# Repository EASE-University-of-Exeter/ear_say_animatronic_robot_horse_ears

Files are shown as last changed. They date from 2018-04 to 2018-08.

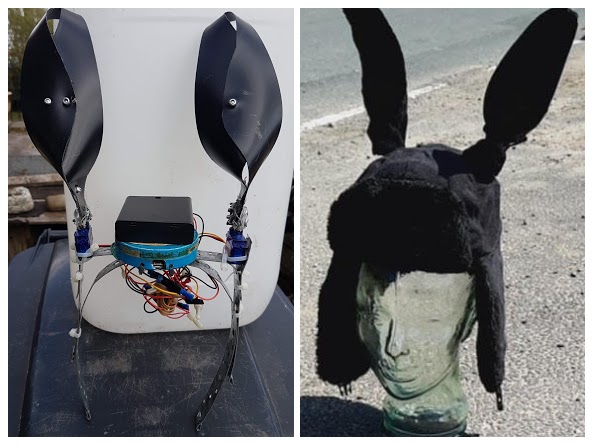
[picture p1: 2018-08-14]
umamimi robotic horse ears - with and without cover.jpg

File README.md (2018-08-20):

umamimi_robotic_horse_ears

================

Author:  Steve North

Author URI:  http://socialsciences.exeter.ac.uk/sociology/staff/north/

License: AGPLv3 or later

License URI: http://www.gnu.org/licenses/agpl-3.0.en.html

Can: Commercial Use, Modify, Distribute, Place Warranty

Can't: Sublicence, Hold Liable

Must: Include Copyright, Include License, State Changes, Disclose Source

Copyright (c) 2018, The University of Exeter

Exploring what it means to be a horse, using expressive ears to communicate both intention and emotion. 

Inspired by the Japanese tradition called ‘Kemonomimi’ (animal eared), which is found in both anime and manga.

This is a project that will reflect on the making of robotic horse ears, living amongst horses using the ears, interspecies communication, becoming 'horse' and even the nature of the quantitative studies that might be conducted to evaluate this artefact.

Umamimi is also inspired by the machines developed for animatronic and puppetry performances. 

Built on a metal framework, with black faux fur covering, two micro servo motors each move an ear independently, in incremental steps, through a maximum range of 180 degrees. An ATmega32u4 processor has been programmed in the Arduino language (a set of C/C++ functions). When the user makes small changes in the inclination of her head, Umamimi’s built-in accelerometer sends these to the software, which responds with programmed (and fully customisable) ear movements: fully forward, fully back, either ear turned outward. When in neutral (meaning that the accelerometer and therefore the device is level), a range of random default ear flicks and movements have been specified.

Horses with different personalities may be configured by selecting a header file (see default.h for a template).

The configurable parameters are as follows:

// Params for random micro default ear movements (when not specifically triggered for specific movement behaviour)

#define PERCENTAGE_TIME_EARS_STATIC 90 // range 1-100% - % of time ears are static

#define DELAY_BETWEEN_EACH_STEP_WHEN_EAR_MOVING 10 // Ear travel time (break each movement into steps and specify pause length between steps)

#define PERCENTAGE_EAR_RANDOM_MICRO_MOVES_TENDING_TOWARDS_UPPER_LIMIT_OF_RANGE 50 // % of ear movements that tend towards upper limits of preset range 

PSEUDOCODE

Loop () 

	{  // Start loop which checks for accelerometer position

	Get the accelerometer position from the microprocessor
	if (position is outside a given threshold limits for pitch and roll - user's head orientation changes triggers ear movement)
		{
			Do something appropriate with one or more ears: move both front, move both back rotate a single ear to outside
		}

	else  // accelerometer position is level /centred or within threshold limits for pitch and roll
		{ 
		
		if (JUST_USER_TRIGGERED_MOVEMENTS)
			{
				new servo/ear positions = defined centre positions for ears
			}
		else // use random micro movements... this is the random microMove algorithm (the automatic ear moves made when the accelerometer is centred)
			{
				Get a random number between 1 and 100
				if (random number > PERCENTAGE_TIME_EARS_STATIC)
					{
						Get a random number between 1 and 100
						if (random number > PERCENTAGE_EAR_RANDOM_MICRO_MOVES_TENDING_TOWARDS_UPPER_LIMIT_OF_RANGE) // restricts the number of higher values, by weighting in favour of lower random values
							{
								restrict RANGE_FOR_RANDOM_MICRO_ANIMATIONS_RELATIVE_TO_CENTRED by the defined ATTENUATION_FACTOR_FOR_MICRO_MOVES_RANGE
							}
						else // choose a random ear position that is within the full RANGE_FOR_RANDOM_MICRO_ANIMATIONS_RELATIVE_TO_CENTRED without 
							{
								Use the full RANGE_FOR_RANDOM_MICRO_ANIMATIONS_RELATIVE_TO_CENTRED
							}
						new servo/ear position = a random number between 1 and 100 and map this to a value in the (full or restricted) RANGE_FOR_RANDOM_MICRO_ANIMATIONS_RELATIVE_TO_CENTRED
					} // close random number was outside PERCENTAGE_TIME_EARS_STATIC... So, generate a random micromove
			
				else // random number was inside PERCENTAGE_TIME_EARS_STATIC
					{
						new servo/ear positions = defined centre positions for ears
					}
	 
			} // use random micro movements
		
		} // close accelerometer position is level /centred or within threshold limits for pitch and roll
		
	if (the new servo/ear positions are the same as the last positions)
		{
			don't move to the same place! // it's a waste of battery life and the wears the servos
		}
	else // the new servo/ear positions are different from the last positions
		{
		if (the new servo/ear positions are user triggered moves / changes in the accelerometer OR the accelerometer is centred immediately after a user triggered move)
			{
				move servos to the new positions (immediately) // this is to make the device responsive to user input, even if the parameters have configured a laconic horse
			}
		else // the moves are random micro movements
			{
				move servo from the previous position to the new position, incrementally with a delay between each increment determined by DELAY_BETWEEN_EACH_STEP_WHEN_EAR_MOVING
			}
		} // close the new servo/ear positions are different from the last positions
	
	} // close loop which checks for accelerometer position

Umamimi - coding setup and config - Arduino IDE and libraries

1. Install Arduino IDE (for Windows, I used: arduino-1.8.5-windows.exe)
2. Install the Adafruit TiCoServo library v1.0.1 in Arduino IDE 1.8.5, do this: Sketch > Include Library > Manage Libraries > search for TiCo and then click Install
Note: Adafruit Circuit Playground v.1.6.8 should be pre-installed in Arduino IDE v.1.8.5
Note: these need to included at the start of a sketch with:
#include <Adafruit_CircuitPlayground.h>
#include <Adafruit_TiCoServo.h>
Note: if needing to test Circuit Playground from Arduino IDE, see File > Examples > Adafruit Circuit Playground
3. To edit Umamimi Robotic Horse ears code, load the sketch umamimi_robotic_horse_ears.ino from the cloned GitHub repository.
4. To connect the Adafruit Circuit Playground in the robotic ears to Arduino IDE (in order to upload the compiled code(, do: Tools > Board > Adafruit Circuit Playground
5. Then do: Tools > Port > <The USB port that the Circuit Playground is connected to. For example: 'COM3 (Adafruit Circuit Playground)'

Umamimi parts list for hardware

1 x AdaFruit Circuit Playground Classic (all-in-one board that has sensors and LEDs)
2 x Tower Pro SG92R Digital Micro Servo
1 x Battery Holder with On/Off Switch for 4 x AA batteries
1 x 2-Pin Male JST-XH Balance Connector with extension wire
1 x Black Micro Suede Trapper Hat
Wire in different colours: 22AWG stranded, outer diameter 1.6mm.
Firm plastic to provide ear shape and rigidity - I upcycled the plastic covers from ringbinder files
1 x metre length of 100% Cotton Velvet - Black - Fabric Velveteen - for ear covering
Velcro tape - to secure inner lining of trapper hat, after opening has been made to insert the device skeleton
Small, elderly, circular metal sticky tape tin (or similar) - to house the Circuit Playground
A roll of metal builders’ band - for umamimi skeleton / head band
Cable ties (with a width narrow enough to go through the holes in the builders’ band) - to fix parts of the skeleton together and to attach the servos, battery holder and Circuit Playground container to the skeleton
Glue gun for ear plastic shaping, sticking black velvet to plastic ears shapers, attaching the servo horn to the ears etc..
Rivet gun - to hold the plastic ear shapers in the stressed ear position (glue on its own didn’t hold!)

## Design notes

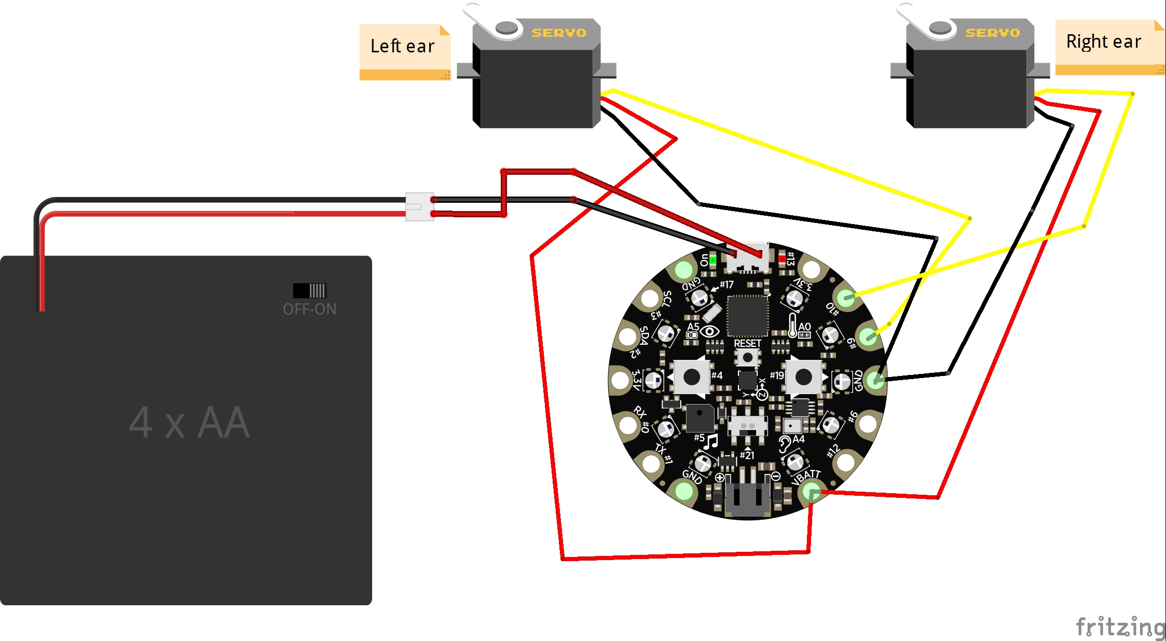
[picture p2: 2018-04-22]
umamimi_robotic_horse_ears- circuit diagram.jpg

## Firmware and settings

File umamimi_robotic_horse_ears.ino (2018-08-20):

/*
umamimi_robotic_horse_ears
================
Author:  Steve North
Author URI:  http://socialsciences.exeter.ac.uk/sociology/staff/north/
License: AGPLv3 or later
License URI: http://www.gnu.org/licenses/agpl-3.0.en.html
Can: Commercial Use, Modify, Distribute, Place Warranty
Can't: Sublicence, Hold Liable
Must: Include Copyright, Include License, State Changes, Disclose Source

Copyright (c) 2018, The University of Exeter
*/

// Leave one (and only one!) of the below horse config files below uncommented, 
// to set random behaviour when centred to a particular horse personality / mood.
// Using default.h as a template. create your own horse and add its profile here.
// For example: dapples.h

// ######### HORSE CONFIG FILES #####################################

#include "default.h"
//#include "free.h"
//#include "duke.h"
//#include "tashe.h"
//#include "smokie.h"
//#include "test_horse_1.h"
//#include "profile_edit_test.h"

// ######### HORSE CONFIG FILES #####################################



#include <Adafruit_CircuitPlayground.h>
#include <Adafruit_TiCoServo.h>

// set next true to turn off randomMicroMovements when accelerometer is centred
#define JUST_USER_TRIGGERED_MOVEMENTS false

#define TIME_EAR_STAYS_IN_POS_AFTER_USER_TRIGGER 1000

// To use microseconds instead of degrees 

#define SERVO_SCALE_MIN 0 //
#define SERVO_SCALE_MAX 1023 //

#define CENTRED_SERVO_LEFT_POSITION 100   // 0 to 1023
#define CENTRED_SERVO_RIGHT_POSITION 900   // 0 to 1023

#define ROLL_LEFT_SERVO_LEFT_POSITION 510   //
#define ROLL_LEFT_SERVO_RIGHT_POSITION 1023   // 

#define ROLL_RIGHT_SERVO_LEFT_POSITION 0   //
#define ROLL_RIGHT_SERVO_RIGHT_POSITION 510   // 

#define PITCH_FORWARD_SERVO_LEFT_POSITION 0   //
#define PITCH_FORWARD_SERVO_RIGHT_POSITION 1023   // 

#define PITCH_BACK_SERVO_LEFT_POSITION 1023   //
#define PITCH_BACK_SERVO_RIGHT_POSITION 0   //

// To use degrees instead of microseconds
/*
#define SERVO_SCALE_MIN -90 //
#define SERVO_SCALE_MAX 90 //

#define CENTRED_SERVO_LEFT_POSITION -60   // 
#define CENTRED_SERVO_RIGHT_POSITION 60   // 

#define ROLL_LEFT_SERVO_LEFT_POSITION 0   //
#define ROLL_LEFT_SERVO_RIGHT_POSITION 90   // 

#define ROLL_RIGHT_SERVO_LEFT_POSITION -90   //
#define ROLL_RIGHT_SERVO_RIGHT_POSITION 0   // 

#define PITCH_FORWARD_SERVO_LEFT_POSITION -90   //
#define PITCH_FORWARD_SERVO_RIGHT_POSITION 90   // 

#define PITCH_BACK_SERVO_LEFT_POSITION 90   //

#define PITCH_BACK_SERVO_RIGHT_POSITION -90   //
*/


// Note the parameters below are the same ones found in the included header files for horse configuration.
// If you comment out all of the header files (higher up), then you can uncomment the next bit and have the configuration inside this file.`

/*

// ##################################

// DEFAULT HORSE!!

// Params for random micro default ear movements (when not specifically triggered for specific movement behaviour)

#define PERCENTAGE_TIME_EARS_STATIC 90 // range 1-100% - % of time ears are static

#define DELAY_BETWEEN_EACH_STEP_WHEN_EAR_MOVING 10 // Ear travel time (break each movement into steps and specify pause length between steps)

#define PERCENTAGE_EAR_RANDOM_MICRO_MOVES_TENDING_TOWARDS_UPPER_LIMIT_OF_RANGE 50 // % of ear movements that tend towards upper limits of preset range 


// ##################################

*/

#define DELAY_AFTER_EACH_LOOP_BEFORE_ACELEROMETER_CHECK 500 // Overall arousal / vigilance / reactiveness / responsiveness level

#define RANGE_FOR_RANDOM_MICRO_ANIMATIONS_RELATIVE_TO_CENTRED 70 // on a scale of 0-100, which is auto mapped to current servo increment range


float X, Y, Z;


// Trigger limits for accelerometer, to create events initiate specific ear move behaviours
#define THRESHOLD_ROLL_LEFT 3   // threshold for...
#define THRESHOLD_ROLL_RIGHT -3   // threshold for...
#define THRESHOLD_PITCH_FORWARD 3   // threshold for...
#define THRESHOLD_PITCH_BACK -3   // threshold for...


// Servo parameters. On Circuit Playground, only pins 9 and 10 are
// supported by the TiCoServo library.
// Servo position can be specified in degrees or in microseconds; library
// can distinguish between the two. The #defines below are reasonable
// min/max pulse durations (in microseconds) for many servos, but for
// maximum control you'll probably need to do some calibration to find
// the optimal range for your specific servos.
#define SERVO_LEFT_PIN    9
#define SERVO_RIGHT_PIN    10

// Note: for TowerPro SG92R servo: Position "0" (1.5ms pulse) is middle, "90" (~2ms pulse) is all the way to the right, "-90" (~1ms pulse) is all the way to the left.
// 0 = 1ms = -90 = -90 degrees
// 511 = 1.5ms = 0 degrees
// 1023 = 2ms = +90 degrees

// ... but actual calibration for the TowerPro SG92R servo, in order to get closer to the 180 degree range, was 0.9ms - 2.5ms

#define SERVO_MIN 900 // 0.9 ms pulse (started with value set at 1000 and calibrated with TowerPro SG92R servo to get further movement range)
#define SERVO_MAX 2500 // 2.5 ms pulse (started with value set at 2000 and calibrated with TowerPro SG92R servo to get further movement range)

Adafruit_TiCoServo servo_left;
Adafruit_TiCoServo servo_right;

// initialise these with the centred positions, so that they are defined on the first accelerometer checking loop
int previous_Servo_left_position_scaled_to_servo_range = CENTRED_SERVO_LEFT_POSITION;
int previous_Servo_right_position_scaled_to_servo_range = CENTRED_SERVO_RIGHT_POSITION;

#define MIN_RANGE_FOR_RANDOM 0
#define MAX_RANGE_FOR_RANDOM 100

#define ATTENUATION_FACTOR_FOR_MICRO_MOVES_RANGE 0.10

#define INCREMENT_BETWEEN_MOVEMENT_STEPS 20


bool isUserTriggeredMove = false;
bool isUserTriggeredReturnToCentreLEFT = false;
bool isUserTriggeredReturnToCentreRIGHT = false;

void setup() {

  servo_left.attach(SERVO_LEFT_PIN, SERVO_MIN, SERVO_MAX);
  servo_right.attach(SERVO_RIGHT_PIN, SERVO_MIN, SERVO_MAX);
  Serial.begin(9600);
  randomSeed(analogRead(0)); // seed random numbers from unused pin 0 on board
  CircuitPlayground.begin();
} // close setup

void loop() {

//Serial.println("loop");
  

  CircuitPlayground.clearPixels();


/*
  X = CircuitPlayground.motionX();
  Y = CircuitPlayground.motionY();
  Z = CircuitPlayground.motionZ();

  Serial.print("X: ");
  Serial.print(X);
  Serial.print("  Y: ");
  Serial.print(Y);
  Serial.print("  Z: ");
  Serial.println(Z);
*/

  // Servo control
  int new_Servo_left_position, new_Servo_right_position, new_Servo_left_position_scaled_to_servo_range, new_Servo_right_position_scaled_to_servo_range;

  isUserTriggeredMove = false;


  if (CircuitPlayground.motionY() > THRESHOLD_ROLL_LEFT) 
  {
  Serial.println("ROLL LEFT");
  CircuitPlayground.setPixelColor(7, 0, 0, 255);

  new_Servo_left_position = ROLL_LEFT_SERVO_LEFT_POSITION;                  // 0 to 1023
  new_Servo_right_position = ROLL_LEFT_SERVO_RIGHT_POSITION;                  // 0 to 1023

  isUserTriggeredMove = true;

  
  } // close ROLL LEFT
  
  else if (CircuitPlayground.motionY() < THRESHOLD_ROLL_RIGHT) 
  {
  Serial.println("ROLL RIGHT");
  CircuitPlayground.setPixelColor(2, 0, 0, 255);

  new_Servo_left_position = ROLL_RIGHT_SERVO_LEFT_POSITION;                  // 0 to 1023
  new_Servo_right_position = ROLL_RIGHT_SERVO_RIGHT_POSITION;                  // 0 to 1023
  
  isUserTriggeredMove = true;


  } // close ROLL RIGHT
  
  else if (CircuitPlayground.motionX() > THRESHOLD_PITCH_FORWARD) 
  {
  Serial.println("PITCH FORWARD"); 
  CircuitPlayground.setPixelColor(4, 0, 0, 255);
  CircuitPlayground.setPixelColor(5, 0, 0, 255);

  new_Servo_left_position = PITCH_FORWARD_SERVO_LEFT_POSITION;                  // 0 to 1023
  new_Servo_right_position = PITCH_FORWARD_SERVO_RIGHT_POSITION;                  // 0 to 1023
  
  isUserTriggeredMove = true;


  } // close PITCH FORWARD

  else if (CircuitPlayground.motionX() < THRESHOLD_PITCH_BACK) 
  {
  Serial.println("PITCH BACK");
  CircuitPlayground.setPixelColor(0, 0, 0, 255);
  CircuitPlayground.setPixelColor(9, 0, 0, 255); 

  new_Servo_left_position = PITCH_BACK_SERVO_LEFT_POSITION;                  // 0 to 1023
  new_Servo_right_position = PITCH_BACK_SERVO_RIGHT_POSITION;                  // 0 to 1023

 isUserTriggeredMove = true;

        
  } // close PITCH BACK

  else 
 
  { // accelerometer is centred
    
 // Serial.println("CENTRED"); 

 

 if (JUST_USER_TRIGGERED_MOVEMENTS)

 {

 
 // next lines makes default ear position fixed, with no micro-animations
 new_Servo_left_position = CENTRED_SERVO_LEFT_POSITION;                  // 
 new_Servo_right_position = CENTRED_SERVO_RIGHT_POSITION;                  //

 } // close JUST_USER_TRIGGERED_MOVEMENTS

else // JUST_USER_TRIGGERED_MOVEMENTS == false ... use randomMicroMoves when accelerometer is centred

{

 // Start: more interesting random movements of ears when no trigger events received (accelerometer is centred)
 

/*************************** START: DEFAULT LEFT EAR ****************************************************/


int randomDefaultEarBehaviour_LEFT = random(MIN_RANGE_FOR_RANDOM,MAX_RANGE_FOR_RANDOM);


if (randomDefaultEarBehaviour_LEFT > PERCENTAGE_TIME_EARS_STATIC && randomDefaultEarBehaviour_LEFT < MAX_RANGE_FOR_RANDOM + 1)

{

// This ear: do RandomMicroMove!
  
// do something...

Serial.println("RANDOM MICROMOVE: LEFT EAR");

// next bit is about deciding how often the full range will be available for random moves within the range
// For exampe: if RANGE_FOR_RANDOM_MICRO_ANIMATIONS_RELATIVE_TO_CENTRED is 10, then values between -10 and +10 should be produced (adjusted to the range of the servos).
// However, PERCENTAGE_EAR_RANDOM_MICRO_MOVES_TENDING_TOWARDS_UPPER_LIMIT_OF_RANGE may restrict the number of higher values,
// by weighting in favour of lower or higher random values. 
// So, if PERCENTAGE_EAR_RANDOM_MICRO_MOVES_TENDING_TOWARDS_UPPER_LIMIT_OF_RANGE is defined as 50%, then 50% of the values will be within the -10 and +10 range,
// but the other 50% will be within a range determined by ATTENUATION_FACTOR_FOR_MICRO_MOVES_RANGE (as a range that is a % of RANGE_FOR_RANDOM_MICRO_ANIMATIONS_RELATIVE_TO_CENTRED.

int fullRangeOrAttenuated = random(MIN_RANGE_FOR_RANDOM,MAX_RANGE_FOR_RANDOM);
int range;

if (fullRangeOrAttenuated > PERCENTAGE_EAR_RANDOM_MICRO_MOVES_TENDING_TOWARDS_UPPER_LIMIT_OF_RANGE)
{
range = RANGE_FOR_RANDOM_MICRO_ANIMATIONS_RELATIVE_TO_CENTRED *  ATTENUATION_FACTOR_FOR_MICRO_MOVES_RANGE;  
}
else
{
range = RANGE_FOR_RANDOM_MICRO_ANIMATIONS_RELATIVE_TO_CENTRED;
}

new_Servo_left_position = 
random(
CENTRED_SERVO_LEFT_POSITION - map(range, 0, 100, SERVO_SCALE_MIN, SERVO_SCALE_MAX), 
CENTRED_SERVO_LEFT_POSITION + map(range, 0, 100, SERVO_SCALE_MIN, SERVO_SCALE_MAX)
);


} // close RadomMicroMove: left ear


else {

// This ear: do static / stay still / don't move!

//Serial.println("RANDOM MICROMOVE: LEFT EAR: CENTRED_SERVO_LEFT_POSITION");

new_Servo_left_position = CENTRED_SERVO_LEFT_POSITION;                  // 

} // close: left ear stays static

/*************************************** END: DEFAULT LEFT EAR ****************************************************/


/*********************************** START: DEFAULT RIGHT EAR ****************************************************/

int randomDefaultEarBehaviour_RIGHT = random(MIN_RANGE_FOR_RANDOM,MAX_RANGE_FOR_RANDOM);


if (randomDefaultEarBehaviour_RIGHT > PERCENTAGE_TIME_EARS_STATIC && randomDefaultEarBehaviour_RIGHT < MAX_RANGE_FOR_RANDOM + 1)

{

// This ear: do RandomMicroMove!
  
// do something...

Serial.println("RANDOM MICROMOVE: RIGHT EAR");


// next bit is about deciding how often the full range will be available for random moves within the range
// For exampe: if RANGE_FOR_RANDOM_MICRO_ANIMATIONS_RELATIVE_TO_CENTRED is 10, then values between -10 and +10 should be produced (adjusted to the range of the servos).
// However, PERCENTAGE_EAR_RANDOM_MICRO_MOVES_TENDING_TOWARDS_UPPER_LIMIT_OF_RANGE may restrict the number of higher values,
// by weighting in favour of lower or higher random values. 
// So, if PERCENTAGE_EAR_RANDOM_MICRO_MOVES_TENDING_TOWARDS_UPPER_LIMIT_OF_RANGE is defined as 50%, then 50% of the values will be within the -10 and +10 range,
// but the other 50% will be within a range determined by ATTENUATION_FACTOR_FOR_MICRO_MOVES_RANGE (as a range that is a % of RANGE_FOR_RANDOM_MICRO_ANIMATIONS_RELATIVE_TO_CENTRED.

int fullRangeOrAttenuated = random(MIN_RANGE_FOR_RANDOM,MAX_RANGE_FOR_RANDOM);
int range;

if (fullRangeOrAttenuated > PERCENTAGE_EAR_RANDOM_MICRO_MOVES_TENDING_TOWARDS_UPPER_LIMIT_OF_RANGE)
{
range = RANGE_FOR_RANDOM_MICRO_ANIMATIONS_RELATIVE_TO_CENTRED *  ATTENUATION_FACTOR_FOR_MICRO_MOVES_RANGE;  
}
else
{
range = RANGE_FOR_RANDOM_MICRO_ANIMATIONS_RELATIVE_TO_CENTRED;
}

new_Servo_right_position = 
random(
CENTRED_SERVO_RIGHT_POSITION - map(range, 0, 100, SERVO_SCALE_MIN, SERVO_SCALE_MAX), 
CENTRED_SERVO_RIGHT_POSITION + map(range, 0, 100, SERVO_SCALE_MIN, SERVO_SCALE_MAX)

);


} // close RadomMicroMove: right ear


else {

// This ear: do static / stay still / don't move!

//Serial.println("RANDOM MICROMOVE: RIGHT EAR: CENTRED_SERVO_RIGHT_POSITION");

new_Servo_right_position = CENTRED_SERVO_RIGHT_POSITION;                  // 

} // close: right ear stays static

/********************************************************* END: DEFAULT RIGHT EAR ****************************************************/


} // close if randomMovesEnabled loop

} // close: accelerometer is centred





   

// send new positions to the servos / ears
writeNewPositionsToServos(new_Servo_left_position,new_Servo_right_position);

delay(DELAY_AFTER_EACH_LOOP_BEFORE_ACELEROMETER_CHECK);
  
}






// ############################################################################




void writeNewPositionsToServos(int new_Servo_left_position,int new_Servo_right_position) {


// Servo control
int new_Servo_left_position_scaled_to_servo_range, new_Servo_right_position_scaled_to_servo_range;

// Scale new positions to servo range

new_Servo_left_position_scaled_to_servo_range = map(new_Servo_left_position, SERVO_SCALE_MIN, SERVO_SCALE_MAX, SERVO_MIN, SERVO_MAX);    // Scale to servo range
new_Servo_right_position_scaled_to_servo_range = map(new_Servo_right_position, SERVO_SCALE_MIN, SERVO_SCALE_MAX, SERVO_MIN, SERVO_MAX);    // Scale to servo range


if (new_Servo_left_position_scaled_to_servo_range != previous_Servo_left_position_scaled_to_servo_range) // check not trying to move servo to same position and ignore if are
{

Serial.print("LEFT: moving to ");
Serial.println(new_Servo_left_position_scaled_to_servo_range); 

if (isUserTriggeredMove)
{

servo_left.write(new_Servo_left_position_scaled_to_servo_range);                               // Move servo

Serial.println("LEFT EAR: user triggered");

isUserTriggeredReturnToCentreLEFT = true;

}

else if (isUserTriggeredReturnToCentreLEFT)
{

servo_left.write(new_Servo_left_position_scaled_to_servo_range);                               // Move servo

Serial.println("LEFT EAR: user triggered return to centre");

isUserTriggeredReturnToCentreLEFT = false;

}


else
{
// move to new position incrementally...
moveLeftEarInStepsTowardsNewServoPosition(previous_Servo_left_position_scaled_to_servo_range, new_Servo_left_position_scaled_to_servo_range);
}

previous_Servo_left_position_scaled_to_servo_range = new_Servo_left_position_scaled_to_servo_range; // Remember the new servo position, as previous

  
} // close: if not the same as previous position

//else { Serial.println("LEFT: already there"); }

if (new_Servo_right_position_scaled_to_servo_range != previous_Servo_right_position_scaled_to_servo_range) // check not trying to move servo to same position and ignore if are
{

Serial.print("RIGHT: moving to ");
Serial.println(new_Servo_right_position_scaled_to_servo_range);

if (isUserTriggeredMove)
{
servo_right.write(new_Servo_right_position_scaled_to_servo_range);                               // Move servo

Serial.println("RIGHT EAR: user triggered");

isUserTriggeredReturnToCentreRIGHT = true;

}


else if (isUserTriggeredReturnToCentreRIGHT)
{
servo_right.write(new_Servo_right_position_scaled_to_servo_range);                               // Move servo

Serial.println("RIGHT EAR: user triggered return to centre");

isUserTriggeredReturnToCentreRIGHT = false;

}

else
{
// move to new position incrementally...
moveRightEarInStepsTowardsNewServoPosition(previous_Servo_right_position_scaled_to_servo_range, new_Servo_right_position_scaled_to_servo_range);
}

previous_Servo_right_position_scaled_to_servo_range = new_Servo_right_position_scaled_to_servo_range;  // Remember the new servo position, as previous


} // close: if not the same as previous position

//else { Serial.println("RIGHT: already there"); }


} // close writeNewPositionsToServos()






void moveLeftEarInStepsTowardsNewServoPosition(int previous_Servo_position, int new_Servo_position) 

{

int tempPos = previous_Servo_position;

if (new_Servo_position > previous_Servo_position)

{

  // ###### GOING UP!!!!! #################

  Serial.print("LEFT EAR travelling UP: ");

  while (tempPos < new_Servo_position - INCREMENT_BETWEEN_MOVEMENT_STEPS)
  {
  tempPos = tempPos + INCREMENT_BETWEEN_MOVEMENT_STEPS;
  Serial.print(tempPos);
  Serial.print(", ");
  servo_left.write(tempPos); 
  delay(DELAY_BETWEEN_EACH_STEP_WHEN_EAR_MOVING);
  }

  servo_left.write(new_Servo_position);

  Serial.println(" ");
  Serial.print("LEFT EAR: Has arrived at: ");

  Serial.println(new_Servo_position);  

}


else // new_Servo_position < previous_Servo_position)

{

 // ###### GOING DOWN!!!!! #################
  
Serial.print("LEFT EAR travelling DOWN: ");
  while (tempPos > new_Servo_position + INCREMENT_BETWEEN_MOVEMENT_STEPS)
  {
  tempPos = tempPos - INCREMENT_BETWEEN_MOVEMENT_STEPS;
  Serial.print(tempPos);
  Serial.print(", ");
  servo_left.write(tempPos); 
  delay(DELAY_BETWEEN_EACH_STEP_WHEN_EAR_MOVING);
  }

  servo_left.write(new_Servo_position);

  Serial.println(" ");
  Serial.print("LEFT EAR: Has arrived at: ");


  
  Serial.println(new_Servo_position);

}

} // close moveLeftEarInStepsTowardsNewServoPosition



void moveRightEarInStepsTowardsNewServoPosition(int previous_Servo_position, int new_Servo_position) 

{

int tempPos = previous_Servo_position;

if (new_Servo_position > previous_Servo_position)

{

 // ###### GOING UP!!!!! #################

Serial.print("RIGHT EAR travelling UP: ");

  while (tempPos < new_Servo_position - INCREMENT_BETWEEN_MOVEMENT_STEPS) 
  {
  tempPos = tempPos + INCREMENT_BETWEEN_MOVEMENT_STEPS;
  Serial.print(tempPos);
  Serial.print(", ");
  servo_right.write(tempPos); 
  delay(DELAY_BETWEEN_EACH_STEP_WHEN_EAR_MOVING);
  }

  servo_right.write(new_Servo_position);

  Serial.println(" ");
  Serial.print("RIGHT EAR: Has arrived at: ");
  Serial.println(new_Servo_position);

}


else // new_Servo_position < previous_Servo_position)

{

 // ###### GOING DOWN!!!!! #################

Serial.print("RIGHT EAR travelling DOWN: ");  

  while (tempPos > new_Servo_position + INCREMENT_BETWEEN_MOVEMENT_STEPS)
  {
  tempPos = tempPos - INCREMENT_BETWEEN_MOVEMENT_STEPS;
  Serial.print(tempPos);
  Serial.print(", ");
  servo_right.write(tempPos); 
  delay(DELAY_BETWEEN_EACH_STEP_WHEN_EAR_MOVING);
  }
  servo_right.write(new_Servo_position);

  Serial.println(" ");
  Serial.print("RIGHT EAR: Has arrived at: ");
  Serial.println(new_Servo_position);

}


} // close moveRightEarInStepsTowardsNewServoPosition

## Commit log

2018-04-22 Various fixes and additions
    Adding Fritz circuit diagram file and JPG
    [ear_say_animatronic_robot_horse_ears.fzz]
2018-05-09 Renaming respository and indiv files
    [umamimi_robotic_horse_ears.fzz]
